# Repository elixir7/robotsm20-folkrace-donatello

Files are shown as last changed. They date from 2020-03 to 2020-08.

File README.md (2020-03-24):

# Donatello Folkrace robot
He look.

He think.

But most importantly

He hack.

# PCB
The robot has 3 different circuitboards:
- 5x Laser sensor boards 
- 1x MCU board
- 1x Motor board
The sensors connects to the MCU board and the MCU board to the motor board.

## Laser sensor board

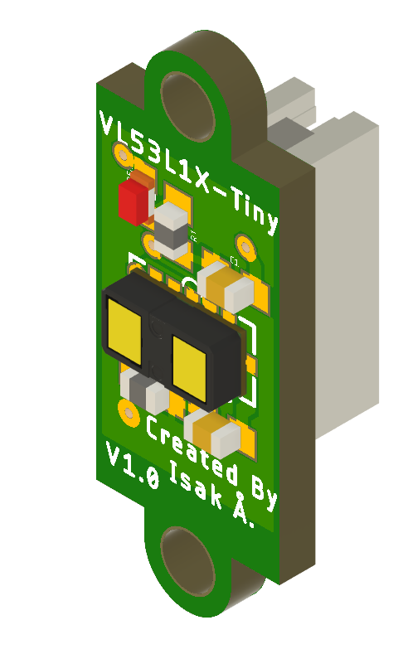
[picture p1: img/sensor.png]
Sensor


A tiny pcb with a laser distance sensor (VL53L1X) creating a 2D lidar by fusion data from multiple sensors.
The sensor has a programmable reciever meaning it is possible to get more distance readings from different angles.

The 5 boards create a 135 deg field of view , ~6.5 deg resolution and  20 data points.

## MCU board

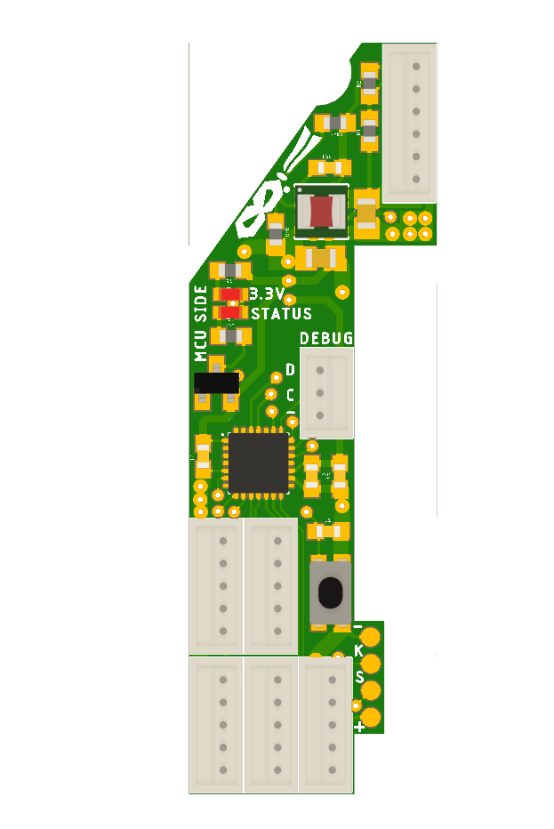
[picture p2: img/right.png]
MCU board


It's the brain of the robot and contains a STM32F031G6 Arm Cortex M0 microcontroller. It also has connectors for all sensors, LED, servo feedback connector and voltage regulator.

## Motor board

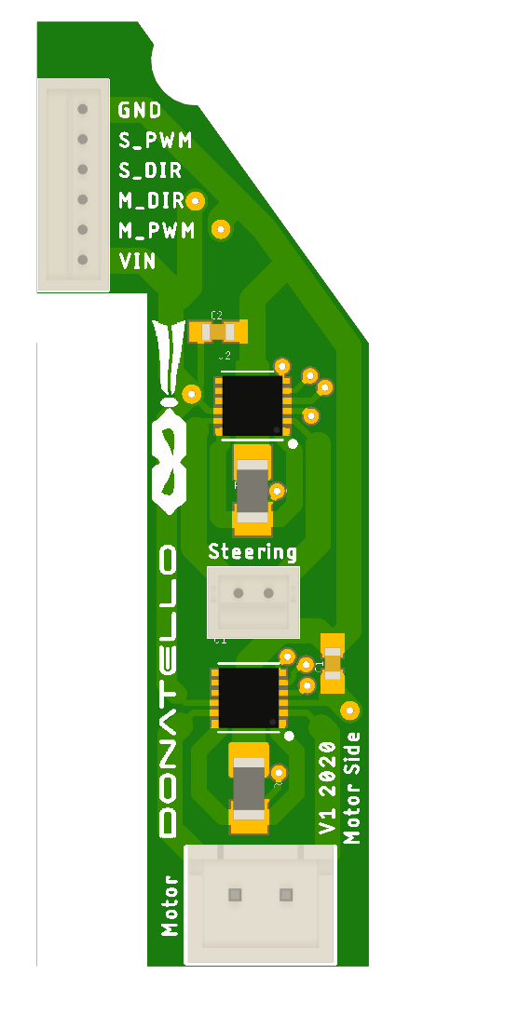
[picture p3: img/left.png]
Motor board


Contains 2 DC motor drivers (MAX14780) and connector the for battery.

# 3D Scan
Point cloud data of the base car, a Kyosho Mini Z Inferno Buggy.

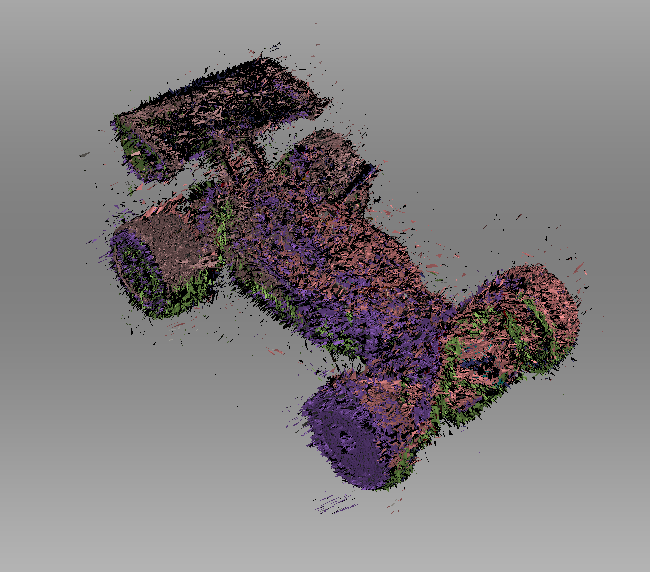
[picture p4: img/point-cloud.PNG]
3D Scan of Kyosho Mini Z Inferno Buggy

 
 Post processed 3D Scan with textures.

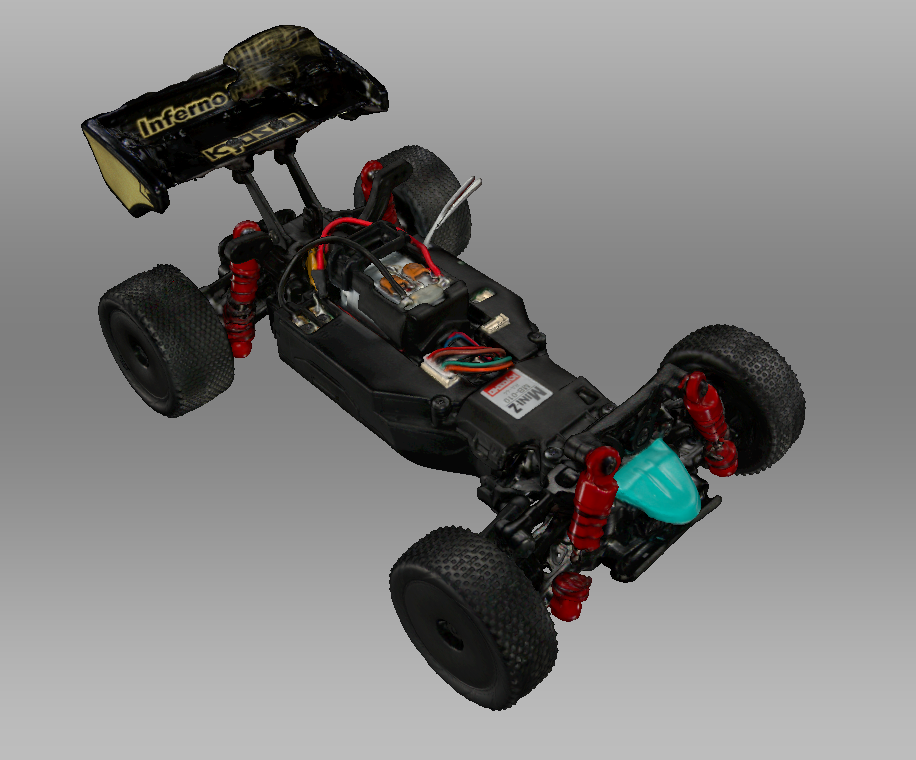
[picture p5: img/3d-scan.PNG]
3D scan with texture


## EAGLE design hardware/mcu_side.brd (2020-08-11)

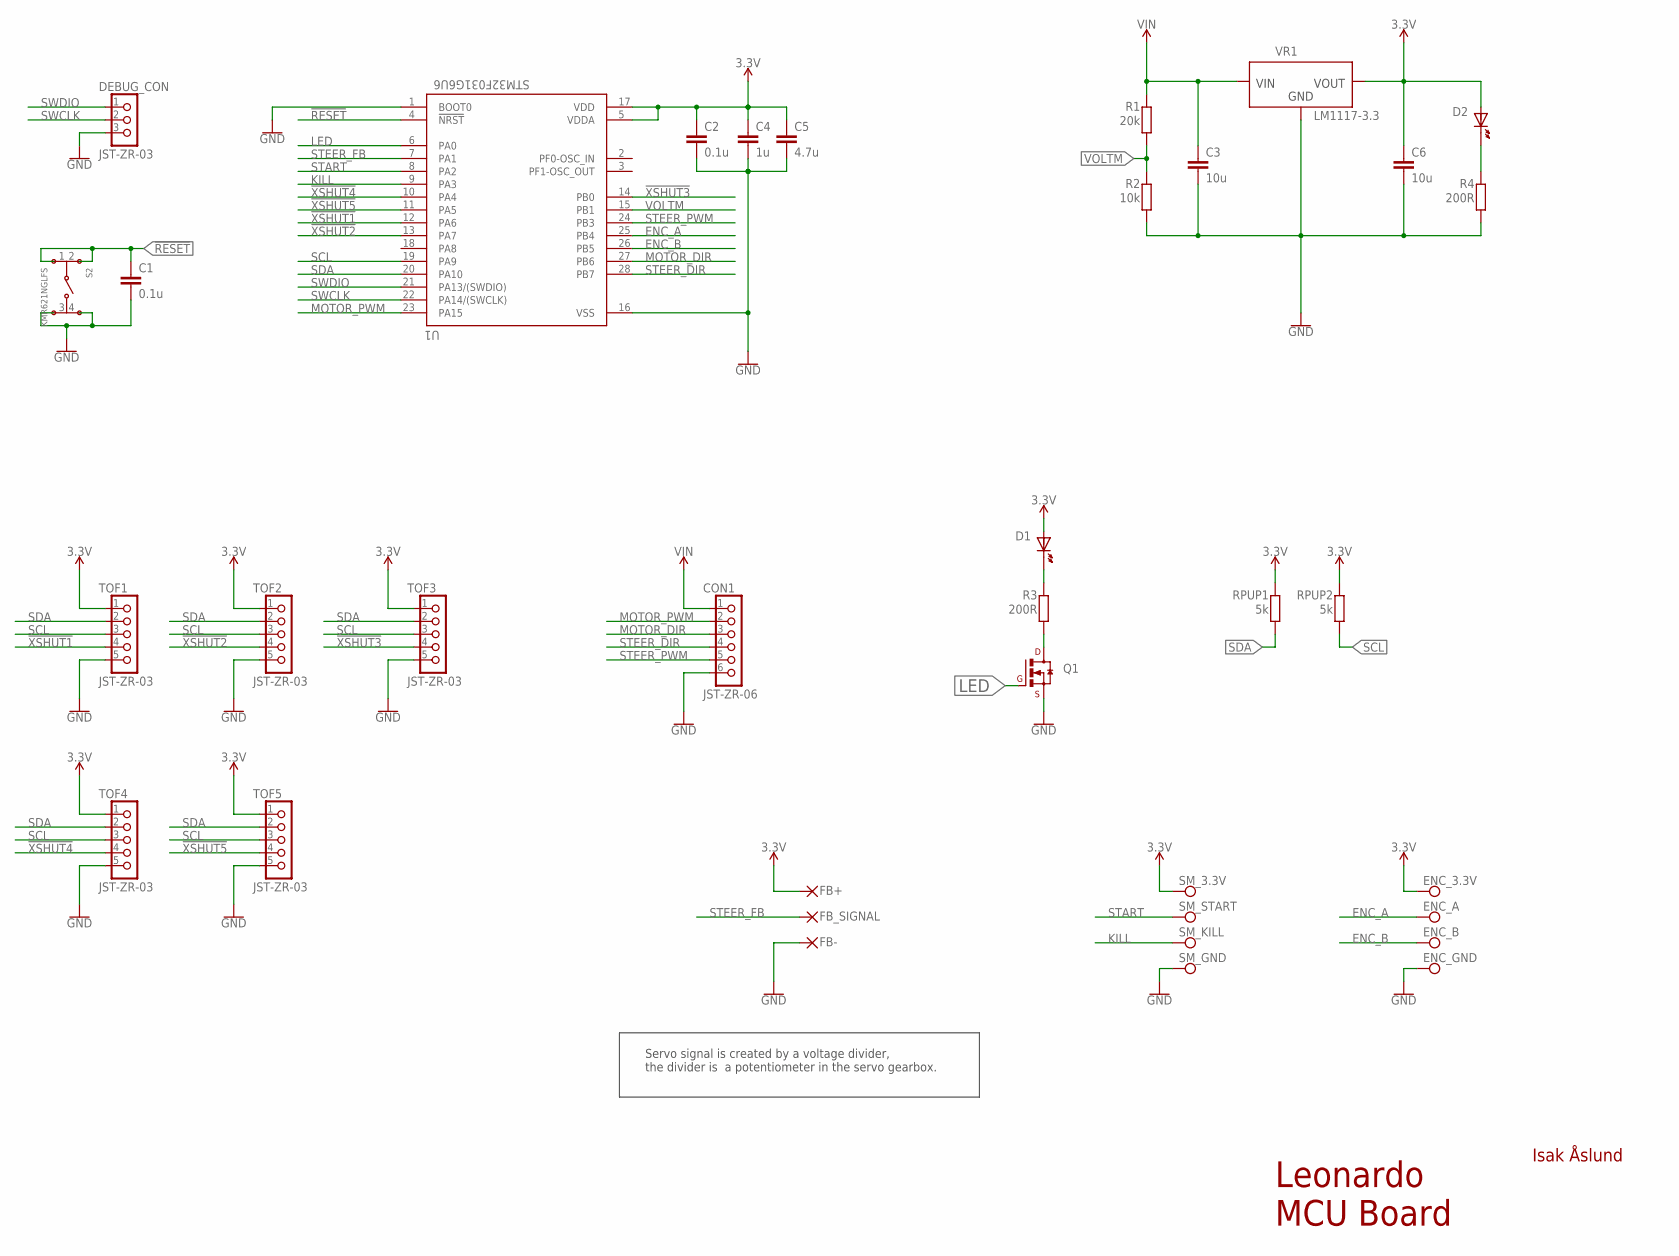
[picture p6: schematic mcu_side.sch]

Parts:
C1, C2: 0.1u; C0603
C3, C6: 10u; C1206
C4: 1u; C0603
C5: 4.7u; C0603
CON1: JST-ZR-06; B6B-ZR
D1, D2: CHIP-LED0603
DEBUG_CON: JST-ZR-03; B3B-ZR
ENC_3.3V: PAD-SMD-ROUND-1.27PAD; PAD.03X.05
ENC_A: PAD-SMD-ROUND-1.27PAD; PAD.03X.05
ENC_B: PAD-SMD-ROUND-1.27PAD; PAD.03X.05
ENC_GND: PAD-SMD-ROUND-1.27PAD; PAD.03X.05
FB+: SMD2; SMD1,27-2,54
FB-: SMD2; SMD1,27-2,54
FB_SIGNAL: SMD2; SMD1,27-2,54
Q1: BSS138LT3G; SOT23
R1: 20k; R0603
R2: 10k; R0603
R3, R4: 200R; R0603
RPUP1, RPUP2: 5k; R0603
S2: KMR621NGLFS
SM_3.3V: PAD-SMD-ROUND-1.27PAD; PAD.03X.05
SM_GND: PAD-SMD-ROUND-1.27PAD; PAD.03X.05
SM_KILL: PAD-SMD-ROUND-1.27PAD; PAD.03X.05
SM_START: PAD-SMD-ROUND-1.27PAD; PAD.03X.05
TOF1, TOF2, TOF3, TOF4, TOF5: JST-ZR-03; B5B-ZR
U1: STM32F031G6U6; QFN50P400X400X60-28N
VR1: LM1117-3.3; SOT230P700X180-4

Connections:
3.3V: C2.1, C4.1, C5.1, C6.1, D1.A, D2.A, ENC_3.3V.P$1, FB+.1, RPUP1.1, RPUP2.1, SM_3.3V.P$1, TOF1.1, TOF2.1, TOF3.1, TOF4.1, TOF5.1, U1.5 (VDDA), U1.17 (VDD), VR1.2 (VOUT), VR1.4 (VOUT)
!RESET: C1.1, S2.1, S2.2, U1.4 (!NRST)
!XSHUT1: TOF1.4, U1.12 (PA6)
!XSHUT2: TOF2.4, U1.13 (PA7)
!XSHUT3: TOF3.4, U1.14 (PB0)
!XSHUT4: TOF4.4, U1.10 (PA4)
!XSHUT5: TOF5.4, U1.11 (PA5)
ENC_A: ENC_A.P$1, U1.25 (PB4)
ENC_B: ENC_B.P$1, U1.26 (PB5)
GND: C1.2, C2.2, C3.2, C4.2, C5.2, C6.2, CON1.6, DEBUG_CON.3, ENC_GND.P$1, FB-.1, Q1.2 (S), R2.2, R4.2, S2.3, S2.4, SM_GND.P$1, TOF1.5, TOF2.5, TOF3.5, TOF4.5, TOF5.5, U1.1 (BOOT0), U1.16 (VSS), VR1.1 (GND)
KILL: SM_KILL.P$1, U1.9 (PA3)
LED: Q1.1 (G), U1.6 (PA0)
MOTOR_DIR: CON1.3, U1.27 (PB6)
MOTOR_PWM: CON1.2, U1.23 (PA15)
unnamed: D1.C (K), R3.1
unnamed: D2.C (K), R4.1
unnamed: Q1.3 (D), R3.2
SCL: RPUP2.2, TOF1.3, TOF2.3, TOF3.3, TOF4.3, TOF5.3, U1.19 (PA9)
SDA: RPUP1.2, TOF1.2, TOF2.2, TOF3.2, TOF4.2, TOF5.2, U1.20 (PA10)
START: SM_START.P$1, U1.8 (PA2)
STEER_DIR: CON1.4, U1.28 (PB7)
STEER_FB: FB_SIGNAL.1, U1.7 (PA1)
STEER_PWM: CON1.5, U1.24 (PB3)
SWCLK: DEBUG_CON.2, U1.22 (PA14/(SWCLK))
SWDIO: DEBUG_CON.1, U1.21 (PA13/(SWDIO))
VIN: C3.1, CON1.1, R1.1, VR1.3 (VIN)
VOLTM: R1.2, R2.1, U1.15 (PB1)

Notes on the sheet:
Leonardo MCU Board
Isak Åslund
Servo signal is created by a voltage divider, the divider is a potentiometer in the servo gearbox.

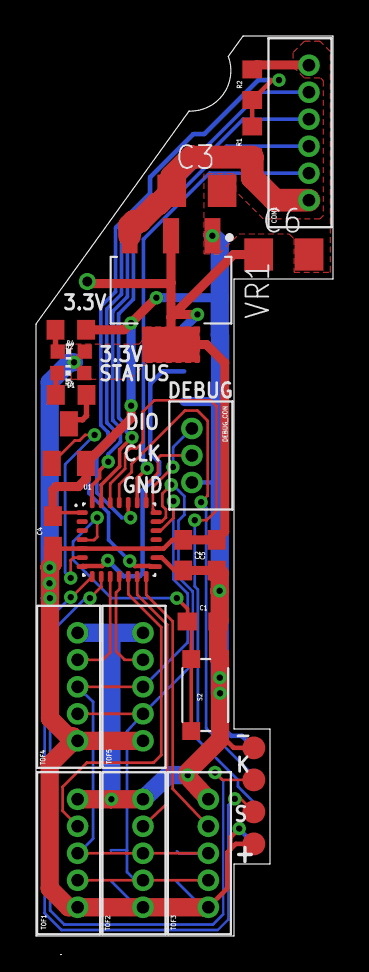
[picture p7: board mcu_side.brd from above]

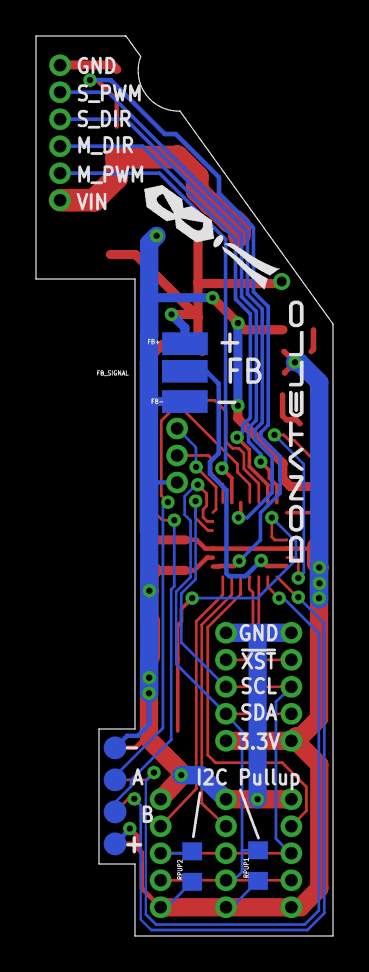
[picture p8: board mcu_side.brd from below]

Board: 2 copper layers, 16.5 x 50.0 mm, 36 parts (9 on the bottom side), 27 nets.

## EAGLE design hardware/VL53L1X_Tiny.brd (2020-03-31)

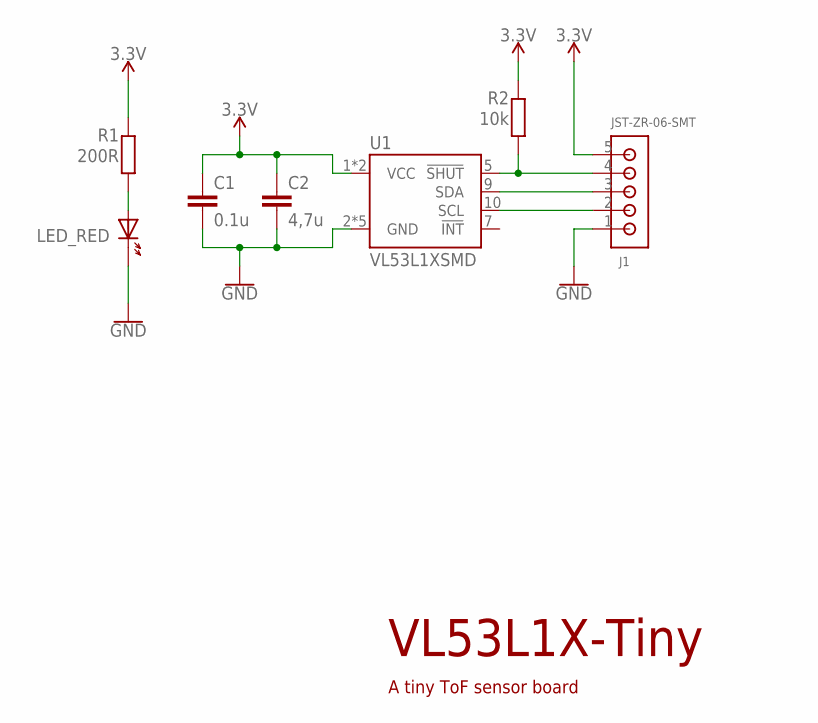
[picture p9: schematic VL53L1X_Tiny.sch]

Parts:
C1: 0.1u; C0603
C2: 4,7u; C0603
J1: JST-ZR-06-SMT; JST_B5B-ZR-SM4-TF_LF_SN_0
LED_RED: CHIP-LED0603
R1: 200R; R0603
R2: 10k; R0603
U1: VL53L1XSMD; VL53L1X

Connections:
3.3V: C1.1, C2.1, J1.5, R1.2, R2.2, U1.1 (VCC), U1.11 (VCC)
!SHUT: J1.4, R2.1, U1.5 (!SHUT)
GND: C1.2, C2.2, J1.1, LED_RED.C (K), U1.2 (GND), U1.3 (GND), U1.4 (GND), U1.6 (GND), U1.12 (GND)
unnamed: LED_RED.A, R1.1
SCL: J1.2, U1.10 (SCL)
SDA: J1.3, U1.9 (SDA)

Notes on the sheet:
VL53L1X-Tiny
A tiny ToF sensor board

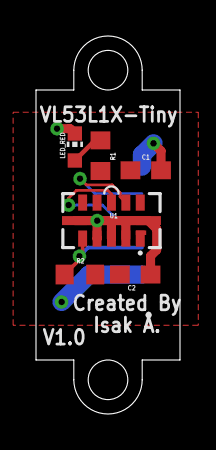
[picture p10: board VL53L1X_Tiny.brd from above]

Board: 2 copper layers, 8.0 x 21.0 mm, 7 parts (1 on the bottom side), 6 nets.

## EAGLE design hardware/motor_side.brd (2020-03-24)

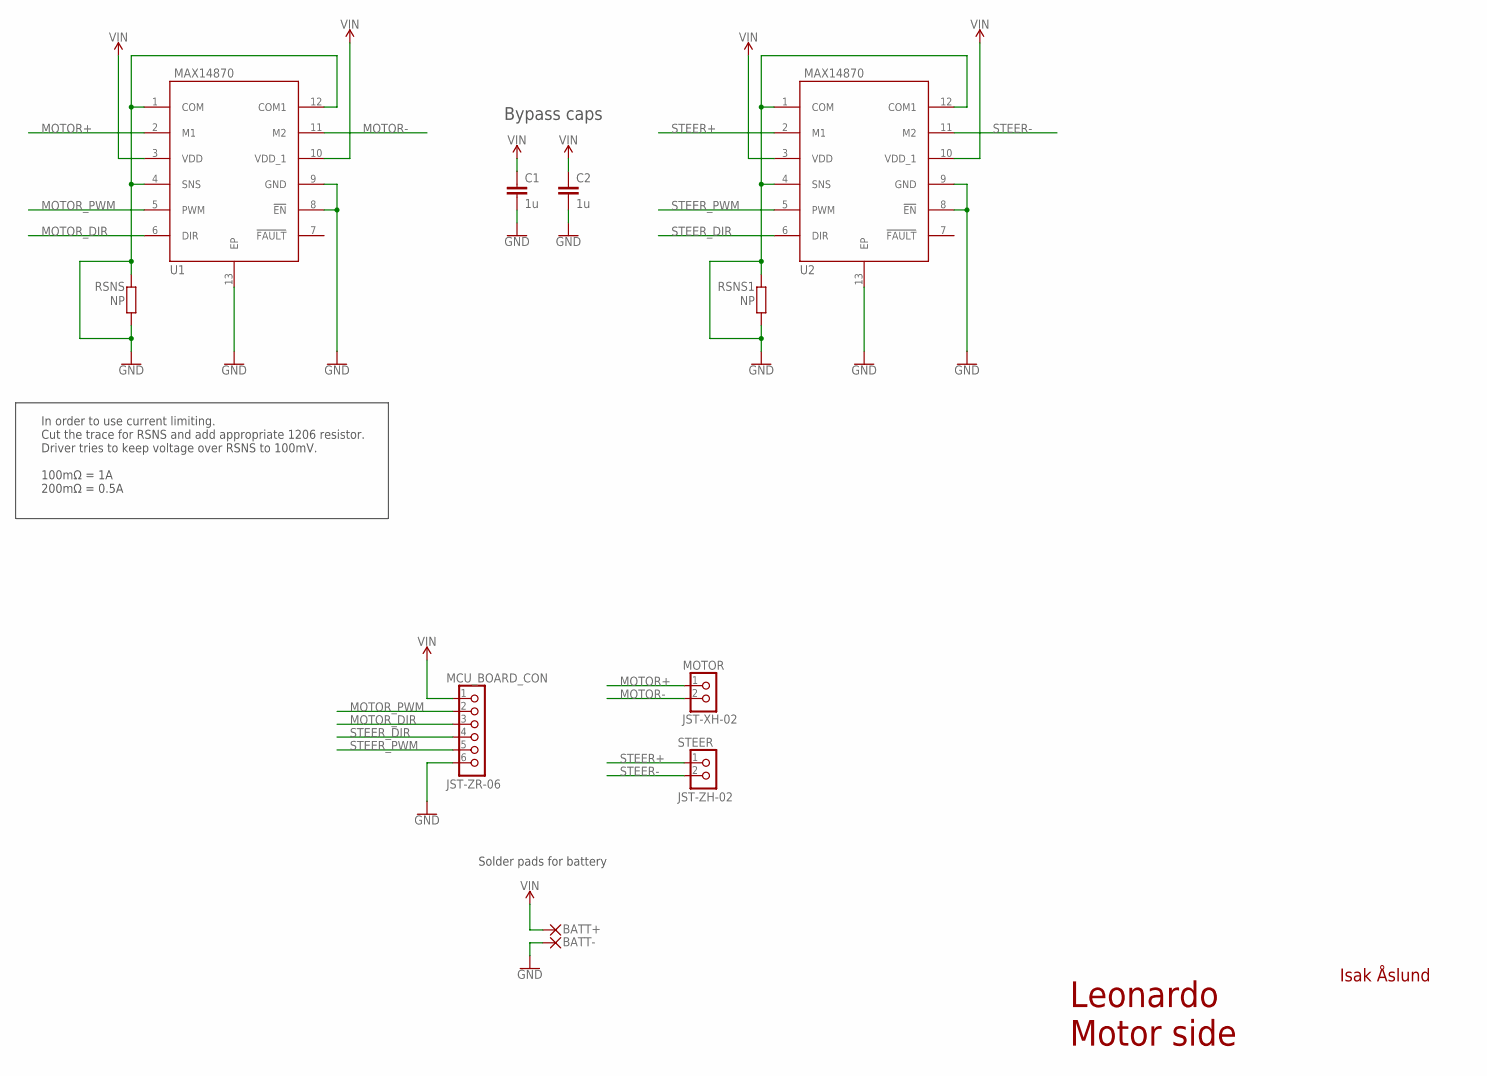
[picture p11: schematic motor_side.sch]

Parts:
BATT+: SMD2; SMD1,27-2,54
BATT-: SMD2; SMD1,27-2,54
C1, C2: 1u; C0603
MCU_BOARD_CON: JST-ZR-06; B6B-ZR
MOTOR: JST-XH-02
RSNS, RSNS1: NP; R1206
STEER: JST-ZH-02; B2B-ZR
U1, U2: MAX14870; 12_TDFN_EP

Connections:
GND: BATT-.1, C1.2, C2.2, MCU_BOARD_CON.6, RSNS.1, RSNS.2, RSNS1.1, RSNS1.2, U1.1 (COM), U1.4 (SNS), U1.8 (!EN), U1.9 (GND), U1.12 (COM1), U1.13 (EP), U2.1 (COM), U2.4 (SNS), U2.8 (!EN), U2.9 (GND), U2.12 (COM1), U2.13 (EP)
MOTOR+: MOTOR.1, U1.2 (M1)
MOTOR-: MOTOR.2, U1.11 (M2)
MOTOR_DIR: MCU_BOARD_CON.3, U1.6 (DIR)
MOTOR_PWM: MCU_BOARD_CON.2, U1.5 (PWM)
STEER+: STEER.1, U2.2 (M1)
STEER-: STEER.2, U2.11 (M2)
STEER_DIR: MCU_BOARD_CON.4, U2.6 (DIR)
STEER_PWM: MCU_BOARD_CON.5, U2.5 (PWM)
VIN: BATT+.1, C1.1, C2.1, MCU_BOARD_CON.1, U1.3 (VDD), U1.10 (VDD_1), U2.3 (VDD), U2.10 (VDD_1)

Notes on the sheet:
Leonardo Motor side
Isak Åslund
In order to use current limiting. Cut the trace for RSNS and add appropriate 1206 resistor. Driver tries to keep voltage over RSNS to 100mV. 100mΩ = 1A 200mΩ = 0.5A
Bypass caps
Solder pads for battery

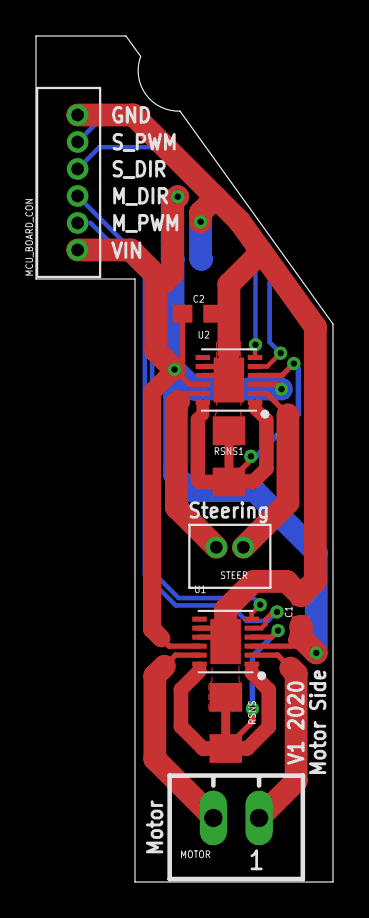
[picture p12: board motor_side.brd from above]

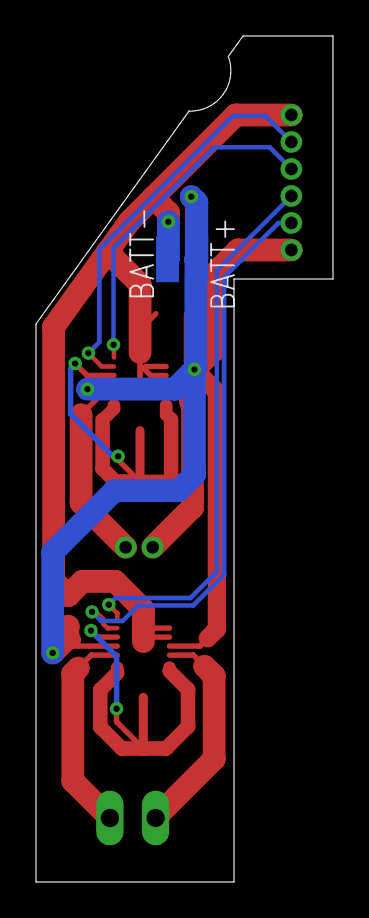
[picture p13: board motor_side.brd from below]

Board: 2 copper layers, 16.5 x 47.0 mm, 11 parts (2 on the bottom side), 10 nets.

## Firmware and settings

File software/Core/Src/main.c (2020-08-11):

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

/* Includes ------------------------------------------------------------------*/
#include "main.h"

TIM_HandleTypeDef htim2;

void SystemClock_Config(void);
static void MX_GPIO_Init(void);
static void MX_TIM2_Init(void);
/**
  * @brief  The application entry point.
  * @retval int
  */
int main(void)
{
  /* MCU Configuration--------------------------------------------------------*/

  /* Reset of all peripherals, Initializes the Flash interface and the Systick. */
  HAL_Init();

  /* Configure the system clock */
  SystemClock_Config();

  /* Initialize all configured peripherals */
  MX_GPIO_Init();
  MX_TIM2_Init();
  /* USER CODE BEGIN 2 */

  //HAL_GPIO_WritePin(MOTOR_DIR_GPIO_Port, MOTOR_DIR_Pin, GPIO_PIN_SET);
  //HAL_TIM_PWM_Start(&htim2, TIM_CHANNEL_1);

  //HAL_GPIO_WritePin(STEER_DIR_GPIO_Port,  STEER_DIR_Pin, GPIO_PIN_SET);
  //HAL_TIM_PWM_Start(&htim2, TIM_CHANNEL_2);

  /* USER CODE END 2 */

  /* Infinite loop */
  /* USER CODE BEGIN WHILE */
  while (1)
  {
    /* USER CODE END WHILE */

    /* USER CODE BEGIN 3 */

		HAL_GPIO_TogglePin(LED_GPIO_Port, LED_Pin);
		HAL_Delay(1000);



/*
		TIM2->CCR1 = 200;
		HAL_GPIO_WritePin(MOTOR_DIR_GPIO_Port, MOTOR_DIR_Pin, GPIO_PIN_SET);
		HAL_GPIO_TogglePin(LED_GPIO_Port, LED_Pin);
		HAL_Delay(1000);

		TIM2->CCR1 = 200;
		HAL_GPIO_WritePin(MOTOR_DIR_GPIO_Port, MOTOR_DIR_Pin, GPIO_PIN_RESET);
		HAL_GPIO_TogglePin(LED_GPIO_Port, LED_Pin);
		HAL_Delay(1000);

		TIM2->CCR1 = 0;
		HAL_GPIO_TogglePin(LED_GPIO_Port, LED_Pin);
		HAL_Delay(1000);
*/
  }
  /* USER CODE END 3 */
}

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


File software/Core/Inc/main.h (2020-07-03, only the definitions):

#define LED_Pin GPIO_PIN_0
#define LED_GPIO_Port GPIOA
#define SWDIO_Pin GPIO_PIN_13
#define SWDIO_GPIO_Port GPIOA
#define SWCLK_Pin GPIO_PIN_14
#define SWCLK_GPIO_Port GPIOA
#define MOTOR_PWM_Pin GPIO_PIN_15
#define MOTOR_PWM_GPIO_Port GPIOA
#define STEER_PWM_Pin GPIO_PIN_3
#define STEER_PWM_GPIO_Port GPIOB
#define MOTOR_DIR_Pin GPIO_PIN_6
#define MOTOR_DIR_GPIO_Port GPIOB
#define STEER_DIR_Pin GPIO_PIN_7
#define STEER_DIR_GPIO_Port GPIOB

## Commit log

2020-03-22 Leonardo V1
    [VL53L1X_Tiny.brd, VL53L1X_Tiny.sch, mcu_side.brd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]
2020-03-23 Add start module
    [mcu_side.brd, mcu_side.sch]
2020-03-24 Logo and name on tPlace/bPlace
    [mcu_side.brd, motor_side.brd, motor_side.sch]
2020-03-24 Added todo before production
    [mcu_side.sch]
2020-03-24 3D Scan and pcb imgs + readme update
2020-03-31 Production ready
    [VL53L1X_Tiny.brd, VL53L1X_Tiny.sch, mcu_side.brd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]
2020-04-15 STM32CubeIDE project setup
    [bom.csv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]
2020-07-03 Motor working
2020-08-11 VReg changed to linear LM1117, 3.3V
    The switching VREG burned the MCU twice..... Switched to an old classic :)
    [bom.csv, mcu_side.brd, mcu_side.sch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]

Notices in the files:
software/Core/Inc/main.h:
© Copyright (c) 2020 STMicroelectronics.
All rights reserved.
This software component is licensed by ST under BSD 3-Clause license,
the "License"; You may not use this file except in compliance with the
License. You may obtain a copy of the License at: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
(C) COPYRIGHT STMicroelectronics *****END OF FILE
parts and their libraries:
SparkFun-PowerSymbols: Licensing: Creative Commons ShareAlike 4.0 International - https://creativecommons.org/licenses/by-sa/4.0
